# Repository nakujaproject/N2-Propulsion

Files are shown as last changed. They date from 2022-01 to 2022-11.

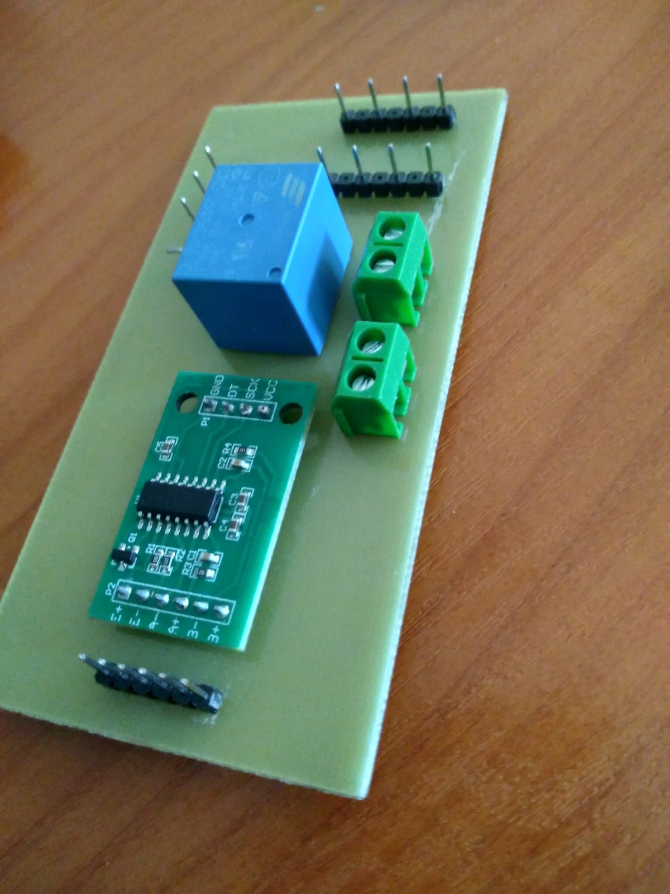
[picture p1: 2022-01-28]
Image gallery/Progress/soldered pcb.jpeg

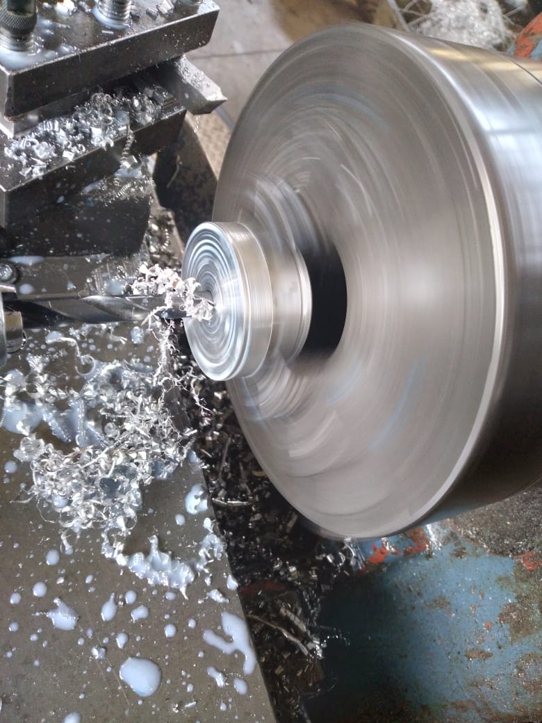
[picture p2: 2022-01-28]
Image gallery/Progress/bulkhead fab.jpeg

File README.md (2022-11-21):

# N2-Propulsion

This is project repo for the propulsion team containing all our design and simulations for the N-2 development

## General info

This project is where our design files for the nakuja N2 Propulsion are held. Different softwares are used for the purpose of development, such as;

* OpenMotor - Fuel Simulations
* Fusion 360 - CAD Designs & PCB Design
* Casing.xls - Excel spreadsheet for casing design parameters
* Ansys Fluent - Computational Fluid Dynamics

## Current directory structure

* **fuel** This contains all simulations for the N2 Fuel, the nozzle designs and casing designs.

* **Launch Pad** Contains all the designs of the lauch pad.

* **Test Stand** Contains the test stand designs, software and recorded data.

* **Important Software** Contains some of the important software used in design.

* **Resources** Contains the resources used in the development of the fuel.

## Pertinent information
* **Data Logging** The present calibration factor for the test stand is ___ .

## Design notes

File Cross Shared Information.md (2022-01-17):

# Cross Shared Information

* **Fuel Casing Outer Diameter**    -    54 mm
* **Fuel Length**                   -    *TBC*

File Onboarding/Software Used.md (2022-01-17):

# Used software

## Motor-Grain Performance simulation

Currently we are using [openMotor](https://github.com/reilleya/openMotor)

## Rocket flight performance

Currently we are using [Openrocket v15.03](https://github.com/openrocket/openrocket/releases/download/release-15.03/OpenRocket-15.03.jar)

## Computer Aided Design

Currently we are using [Inventor 2020](https://knowledge.autodesk.com/support/inventor/learn-explore/caas/CloudHelp/cloudhelp/2020/ENU/Inventor-WhatsNew/files/GUID-8126E8EE-422A-4DEF-9B14-513D87BD4122-htm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's,the%20release%20of%20Inventor%202020.&text=Inventor%202020%20delivers%3A,a%20modernized%20look%20and%20feel.)

## Analysis

For fluid analysis we are using [CFD 2019](https://knowledge.autodesk.com/support/cfd/troubleshooting/caas/downloads/content/autodesk-cfd-2019-download-and-install-help-documentation.html)

The Autodesk fusion version we are using is [Fusion 360](https://www.autodesk.com/products/fusion-360/free-trial)

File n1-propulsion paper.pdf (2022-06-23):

# Development of Solid Propellant Motor For Low Altitude Model Rockets

Abstract This paper describes the design, analysis, and testing of a solid propellant rocket motor designed to propel a model rocket to an apogee of 50 meters. The motor and the propulsion system had to be integrated into an airframe with a small payload thus had to provide enough thrust to reach the desired altitude yet remain compact and lightweight. All this had to be done with the constraint of only using locally sourced materials.
OpenMotor software was used in simulating the motor performance of the motor. ANSYS Fluent was used to analyze the flow within the motor chamber and nozzle. Data from static tests are presented in this paper for the different motor designs and fuels tested. Sugar was used as fuel in the rocket motor with variations being made on the sugar types: Sucrose and Dextrose. The oxidizer used was Potassium nitrate. The paper presents a comparison of the different fuels used as well as the methods used in the preparation.
The selected motor was able to produce an average thrust of 35 Newtons with a peak thrust of 48 Newtons, which was able to propel the rocket to an apogee of 34 meters.

Keywords Solid propellant, static fire test, thrust curve.

30 1. Introduction
Rocket launches are a common scenario in the present 32 day with giant companies like SpaceX and Blue Origin 33 competing to pioneer space exploration [1][2]. While 34 this technology is fascinating, it has been growing for 35 decades [3]. However, modern rocketry became more
pronounced in the 20th 36 | Century [4]. | Robert H. Goddard,
37 an American, conducted experiments with solid and 38 liquid rocket propellants. He managed to fly a liquid-39 propelled rocket to an altitude of 12.5 meters in 1926 40 [5]. Jack Parsons, an American aerospace engineer in 41 1942, invented modern solid rocket propellant rockets 42 [6]. He substituted double-base propellant with asphalt 43 and potassium perchlorate. Most recently, these 44 propellants have been used in orbital space flights and 45 as boosters on rockets.
46 Our rocket development team, the Nakuja project,seeks 47 to build a low altitude solid motor propellant rocket to 48 fly it to an altitude of 50 m. Because solid rocket motors 49 are safer to work with and can last longer without 50 degradation, they were the appropriate choice for this 51 research. In this study, we conduct simulations to find

52 out the appropriate mixtures and grain size to be cast in 53 the solid rocket motor.
54 Based on the parameters obtained from the simulation, 55 we design and cast the solid rocket motor. To enhance 56 the motor performance, we also fabricate the nozzle. 57 Finally, we test and analyze the propellant’s 58 performance.
59 2. | Simulation
60 | The simulation was conducted to visualize some
61 abstract concepts, generate design parameters, create 62 step-by-step progression for iterative design as well as 63 generate safety guidelines. Autodesk Inventor was used 64 to model casing design and material analysis [9]. This 65 was done by utilizing the finite element analysis feature of 66 Autodesk Inventor. There was a need to strike a balance 67 between weight and strength. The propellant performance 68 was simulated using OpenMotor with the parameters 69 shown in Table I. The set parameters resulted in a 70 nozzle cross section as shown in Fig. 1.
71
72 | Table I
73 | Simulation SETTINGS FOR Openmotor
Parameter | Value

Throat Diameter | 10 mm
Exit Diameter | 22 mm
Efficiency | 0.85
Divergence Half Angle | 15 degrees
Convergence Half Angle | 35 degrees
Throat Length | 5 mm
Slag Build-up coefficient | 0 (m•Pa)/s
Throat Erosion coefficient | 0 m/(Pa•s)
Expansion Ratio | 4.84
74

75

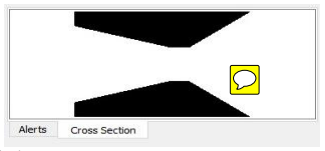
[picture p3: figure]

76 Fig 1. Nozzle cross-section designed by OpenMotor 77
78 The parameters of the propellant shown in Table I 79 include propellant grain length, grain diameter, and 80 combustion chamber diameter. A variation of these 81 parameters outlined the iterative construction and 82 testing path. The output of OpenMotor is a curve of the 83 instantaneous thrust against time as shown in Fig. 2. 84 This data coupled with the initial weight of the motor 85 and propellant are combined to form a .eng file. This 86 file can be used with OpenRocket to simulate rocket 87 flight.

88

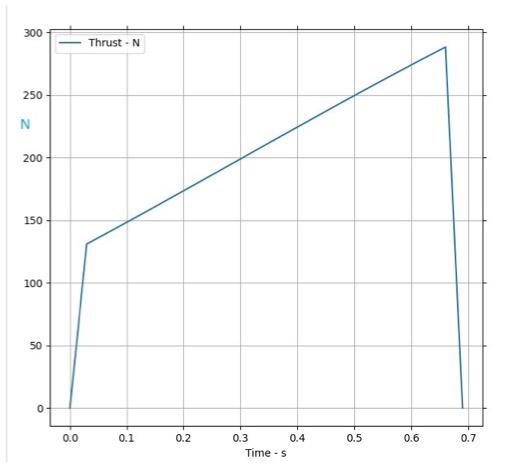
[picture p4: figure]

89 | Fig 2. Thrust curve generated by OpenMotor
90
91 The | various | motor | configurations | developed
92 throughout the iterative design process are illustrated in 93 Table II.
94
95 | | | Table II
96 | Imported .eng files from openRocket
Designatio | Total
n | Impulse (Ns)
Diamete | Lengt
r | h
(mm) | (mm)

F87
F46
F94
F65
F64
G47
G146
G108

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
G106 | 115 | 40 | 200
G152 | 119 | 40 | 200
G168 | 121 | 40 | 200
G117 | 131 | 40 | 200
G114 | 133 | 40 | 200
G186 | 140 | 40 | 200
97
98 Fig. 3 shows the simulated positioning of the motor 99 inside the rocket during simulation.
100

101

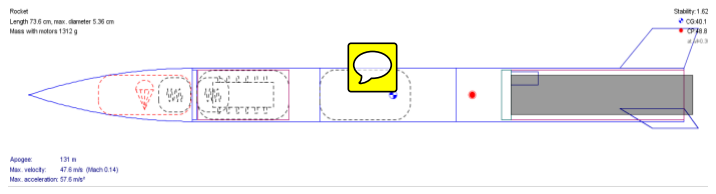
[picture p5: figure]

102 | Fig. 3. Image of rocket with the motor in place
103
104 The results from simulations conducted are highlighted 105 in Table III. The parameters that were critical to 106 development are the apogee and time of flight.
107
108 | Table III
109 | Simulation results from OpenRocket
Name | Apogee (m) | Time of flight (s)
V6- KNSU | 107 | 37.2
V6-KNSU-nozzled | 358 | 114
V7-KNSU | 134 | 45.4
V7-KNSU-nozzled | 450 | 142
V8-KNDX | 137 | 46.6
V8-KNDX-nozzled | 401 | 127
V9-KNDX | 134 | 45
110

111 3. Design
112 During iterative testing and development, the geometry 113 of the motor changed. The initial motor design was as 114 illustrated in Fig. 4.
115

116
117

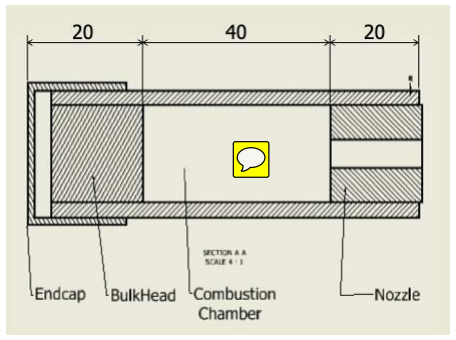
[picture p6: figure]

118 | Fig. 4. Initial motor design
119
120 | The final design of the motor was as illustrated in Fig.

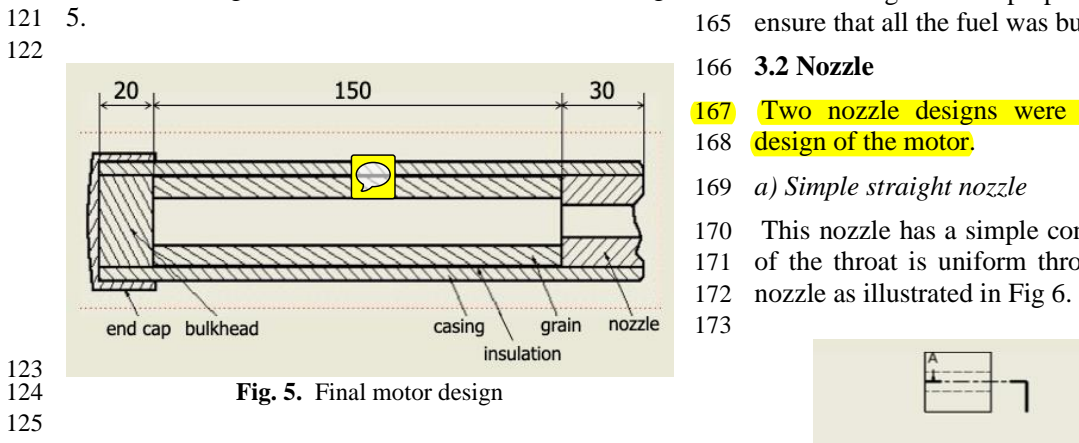
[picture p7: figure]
Fig. 5. Final motor design; 166 3.2 Nozzle; 168 design of the motor.; 169 a) Simple straight nozzle; 172 nozzle as illustrated in Fig 6. 173

126 | The different parts of the motor design can be broken
127 down as follows.

128 Casing

129 This part forms the body of the motor and is hollow to 130 accommodate the propellant grain and the nozzle. The 131 casing has some functional requirements, which 132 include; it should be able to withstand the high 133 temperatures and pressure of propellant combustion and
134 it | should | be | lightweight. | The | non-functional
135 requirements of the casing include that it should be 136 locally available and should be cheap to facilitate 137 iterative testing. The research was conducted on several 138 materials and two were shortlisted (i.e., Aluminum and 139 PVC). They both met the design requirements but PVC 140 was chosen, as it was cheaper, more readily available, 141 and easier to work with. The first iterations of the motor 142 used ¾-inch PVC pipe of various lengths. The length of 143 the final motor casing was chosen to be 200 mm. The 144 PVC pipe used was PN25 meaning it has a pressure 145 rating of 2.5 MPa. The pipe had an outer diameter of 40 146 mm and an inner diameter of 31 mm. The length of the 147 propellant grain heavily influenced this length. The 148 hollow tube would be capped by a PVC fitting called an

149 end cap and some hydraulic cement forming the 150 bulkhead. The other end of the hollow tube would house 151 the nozzle.

152 3.1 Propellant
153 The research was conducted and the team settled on 154 three possible propellants for development. All the 155 propellants had a simple combination of oxidizer, fuel, 156 and catalyst. For all the three propellants Potassium 157 Nitrate was chosen as the oxidizer and Iron III oxide 158 was chosen as the catalyst. Potassium Nitrate was 159 chosen because of its fair performance and availability. 160 The three propellants chosen were; 1. Potassium Nitrate 161 and Sucrose (KNSU) 2. Potassium Nitrate and Dextrose 162 (KNDX) 3. Potassium Nitrate and Sorbitol (KNSB). 163 The oxidizer to fuel ratio for all three fuels was 65 to 164 35. Meaning that the propellant was oxidizer rich to 165 ensure that all the fuel was burnt during combustion.
167 | Two nozzle designs were settled upon during the
170 | This nozzle has a simple construction as the diameter
171 of the throat is uniform throughout the length of the

174

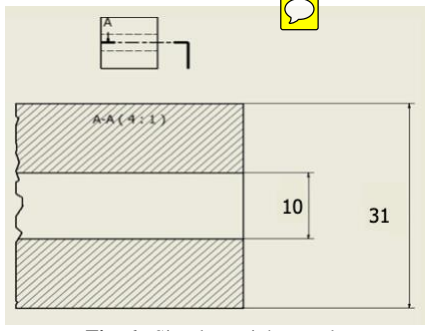
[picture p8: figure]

175 | Fig. 6. Simple straight nozzle
176 b) de Laval nozzle

177 This nozzle consists of a converging section, throat, 178 and diverging section as illustrated in Fig. 7 [10].
179

180

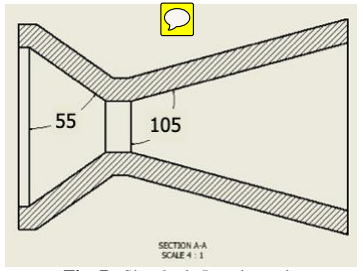
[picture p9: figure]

181 | Fig. 7. Simple de Laval nozzle
182
183 The converging section of the nozzle causes the gases 184 produced during combustion to accelerate linearly 185 towards the throat. At the throat, the gases achieve sonic 186 velocity and in the diverging section, the pressure of the 187 gases is reduced while conversely increasing the 188 velocity of the gases.

189 c) Nozzle CFD Analysis

190 A two-dimensional CFD analysis was carried out for 191 the nozzle design. From the resulting contours a
192 symmetry model was generated. Double precision was 193 used with 2 parallel processors selected. The solver 194 type was density-based and the flow was set to
195 axisymmetric. The energy equation was turned on and 196 the viscous model was set to k-epsilon (k-ϵ). To
197 simulate a turbulent flow k-ϵ (Realizable) viscous 198 model is used. The properties of the working fluid are 199 stated in Table IV.
200
201 | Table IV
202 | Properties of Air
Property | Air
Density | Ideal Gas
Specific Heat | 1006.43 (J/kg.K)
Thermal
conductivity

0.0242 (W/m.K)

Molecular Weight | 28.966 (kg/kmol)
Viscosity | Sutherland
203
204 The boundary conditions used are shown in Table V. 205
206 | Table V
207 | Boundary Conditions
Property | Value
Pressure inlet total gauge
pressure

2268000 (Pa)

Initial gauge pressure | 2267000 (Pa)
Inlet temperature | 1200 (K)
Pressure of operating
conditions

0 (Pa) (absolute)

Outlet pressure, Temperature 39365 (Pa), 243 (K) 208
209 A structured mesh was generated for the profile 210 resulting in 2587 nodes and 2410 elements. Face

211 meshing was applied on each of the five subsections 212 with adaptive sizing and a resolution of 7. The
213 resulting mesh is shown in Fig. 8.
214

215

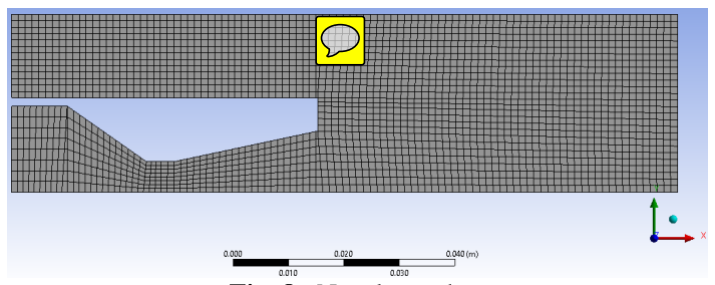
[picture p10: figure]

216 | Fig. 8. Nozzle mesh
217
218 The pressure contours generated are in Fig. 10. The 219 model used was k-ϵ. For gas, the pressure obtained for 220 the k-ϵ is 11.5% higher than the theoretical value [12]. 221

222

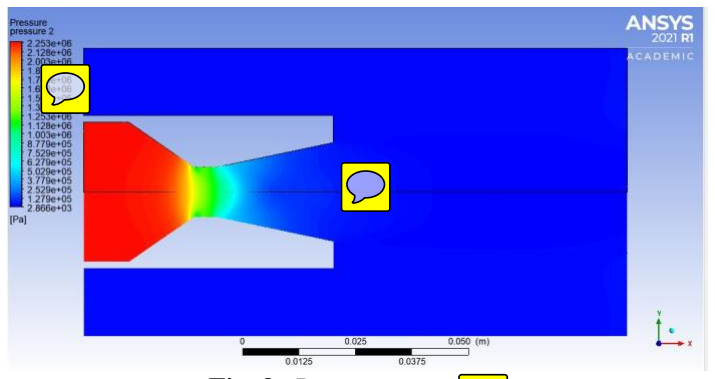
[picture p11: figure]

223 | Fig. 9. Pressure contour
224
225 From the results in Fig. 9, it was observed that the 226 pressure decreases from the convergent side of the 227 nozzle and no shocks are observed to form in the nozzle 228 which was ideal.
229 The contours generated for the velocity are shown in 230 Fig. 11. For Air velocity obtained in k-ϵ model, it is 231 2.5% lower than the theoretical value [12].
232

233

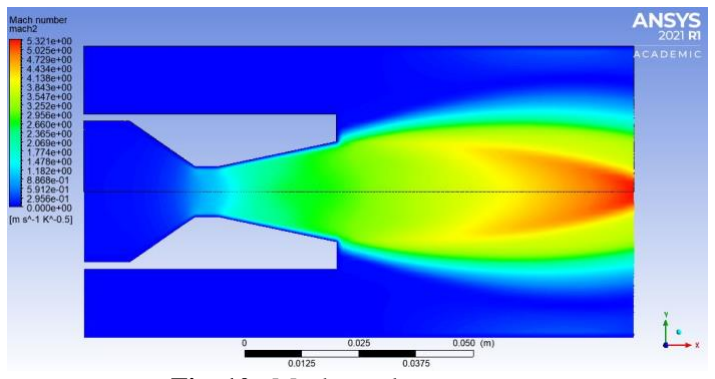
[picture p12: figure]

234 | Fig. 10. Mach number contour
235
236 The Mach number of the fluid as shown in Fig. 10 237 increases along the length of convergent-divergent 238 nozzles due to conservation of momentum in the fluid.

239 4. Fabrication

240 4.1 Casing

241 The casing was fabricated as follows: From V1 to V5 242 (earlier versions of the motor) the casing was made by 243 cutting to size a 3/4 inch PVC pipe. The length of the 244 pipe varied depending on the required geometry of the 245 specific motor. For later versions, the PVC pipe used 246 had an outer diameter of 40 mm with the length of each 247 being cut at 200 mm. The cut ends were smoothened 248 and squared using sanding paper.
249
250 4.2 Propellant
251 During the development, alterations were made to the 252 method of preparing the propellant. The process started 253 by obtaining the fuel and oxidizer. For sucrose we used 254 icing sugar as the particles are very small, for dextrose 255 we used glucose (dextrose monohydrate) and sorbitol 256 was obtained as sorbitol 70% solution. Potassium 257 Nitrate was obtained with a purity of 99% from local 258 chemical suppliers. Iron III oxide was obtained from a 259 chemical supplier at 99% purity. To obtain solid 260 sorbitol from the solution, the sorbitol solution was 261 heated in a pan using an electric heater for 15 minutes 262 at 150 degrees Celsius.
263 The weight of the required propellant was obtained 264 from OpenMotor. The solid components were first 265 blended using a blender and sieved to obtain the finest 266 particles. They were then weighed out using an 267 electronic scale and mixed in the ratio stated above 268 (65:35; O: F) the catalyst was added as 1 % of the 269 oxidizer and fuel mixture. The mixture was placed in a 270 plastic can and shaken vigorously. For sorbitol, the 271 solid obtained was in the form of a slurry and was used 272 as-is.
273 The first iterations of propellant development involved 274 dry packing this propellant mixture into the casing 275 using a mallet and a wooden rammer. The propellant 276 mixture was added in small amounts into the casing and 277 each time it was packed in using the rammer and the 278 mallet. When the desired height of the propellant was 279 achieved, a drill bit was used to create a combustion 280 chamber. The size of the combustion chamber 281 depended on the required grain geometry.
282 For further motors, the propellant grain was prepared 283 by casting. Casting involves heating the propellant 284 mixture until it melts and pouring it into a mold to 285 obtain the desired shape. The grain is left to solidify and 286 then removed from the casting apparatus. The casting 287 process was done using an electric heater, a pan, and 288 coring rods and tubes. A coring rod is a cylindrical piece 289 of metal with a chosen size all through. A coring tube is 290 made by cutting 150 mm of PVC pipe and then lining 291 the inside with cardboard paper. The paper serves as a

292 cover for the solid propellant as well as an insulator to 293 the casing during combustion.
294 The casting process began by preheating the pan and 295 then adding about half the propellant mixture to the pan. 296 Using a wooden spoon, the mixture was stirred until it 297 started to melt. More of the mixture was added at this 298 point. The propellant was heated to a casting 299 temperature of 145 °C for KNSU, 135 °C for KNSB and 300 KNDX. The propellant was then poured into the casting 301 tube and the coring tool was inserted to make a 302 combustion chamber. The coring tool was left in for a 303 sufficient time; 3 minutes for KNSU, 10 minutes for 304 KNDX, and 20 minutes for KNSB; until the propellant 305 began to solidify. At this point, the coring tool was 306 removed and the grain was left to cool in a desiccator. 307 The desiccator was constructed using a simple lunch 308 box in which a sufficient amount of Fused calcium 309 chloride was placed.
310 The grain was left to cool until it was fully solidified. 311 For KNSU it would take roughly 3 hours, for KNDX it 312 would take about 24 hours and for KNSB it would take 313 48 hours Once the grain had solidified it was ready for 314 firing. An image of the casting process is illustrated in 315 Fig 11.
316

317

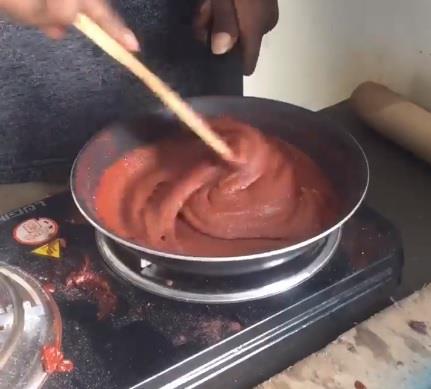
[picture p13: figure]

318 | Fig. 11. Casting process
319
320 The final grain obtained was red for all three propellant 321 types as a result of the Iron III oxide. Fig. 12 shows the 322 grain in the casting tube and casting case after removing 323 the coring rod.
324

325

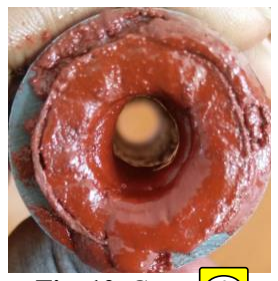
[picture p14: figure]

326 | Fig. 12. Cast grain
327 4.3 Nozzle
328 Both the straight and de Laval nozzles were made using

329 hydraulic cement. The cement is fast setting and only 330 requires to be mixed with water.

331 a) Straight nozzle

332 The straight nozzle was constructed by placing a finite 333 amount of cement into an open end of the cut PVC pipe 334 and letting it solidify. A drill bit was then used to make 335 a hole of the required diameter in the cement.

336 b) de Laval nozzle

337 This nozzle was first made by painting the inside of the 338 casing with acrylic paint. This was done to enhance the 339 cohesion of the hydraulic cement and the walls of the 340 PVC pipe. The paint was allowed to dry overnight. The 341 converging side was made using a 3D printed part 342 displayed in Fig. 13.
343

344

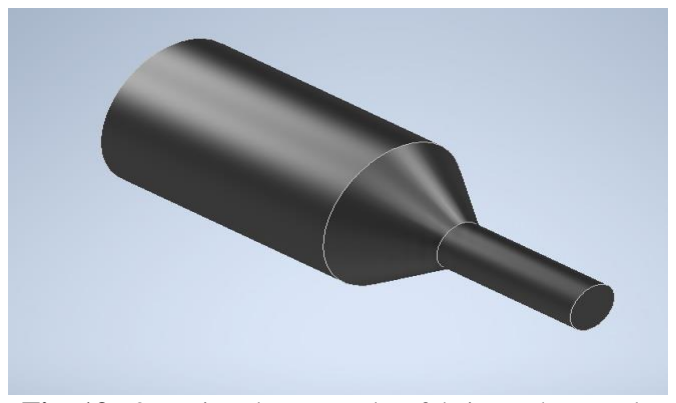
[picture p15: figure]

345 Fig. 13. 3D printed part used to fabricate the nozzle 346
347 The cement was first mixed with water. The part was 348 pushed in through the unpainted side until the tip of the 349 part was flush with the painted end of the pipe. The 350 cement was then poured onto the cavity formed and 351 then allowed about 3 minutes to solidify. The piece was 352 then forced out using a screwdriver and a hammer. The 353 diverging side was made by using a scraper to remove 354 the cement until the required angle of 15 degrees was 355 obtained. The completed nozzle was as shown in Fig. 356 14.
357

358

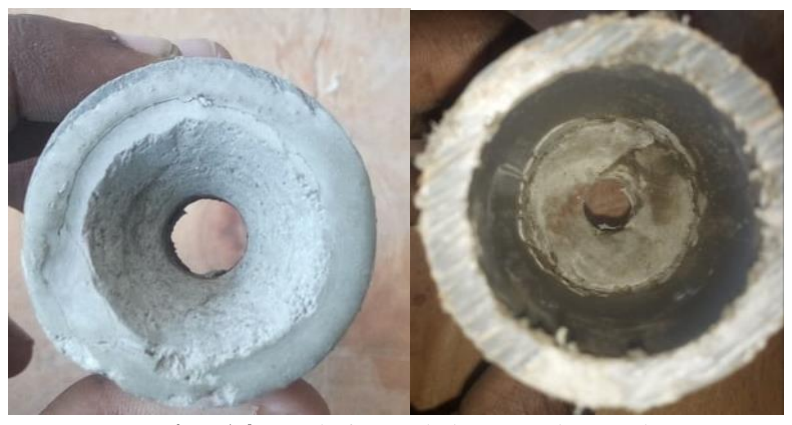
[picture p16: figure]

359 | Fig. 14. Fabricated de Laval nozzle
360 | (left: diverging side, right: converging side)
361
362 4.4 Assembly
363 The assembly of the motor was done by first 364 constructing the nozzle as described above. The grain

365 obtained after casting was placed in the casing with the 366 constructed nozzle. The open end of the casing was then 367 sealed with hydraulic cement. To reinforce this a PVC 368 end was added. The PVC end cap is a PVC fitting of an 369 internal diameter of 40 mm and an external diameter of 370 50 mm. The end cap was attached using PVC tangit 371 glue. The external surface of the casing was buffed 372 using sandpaper and the ends were made square. Tangit 373 glue was applied to the casing and the internal side of 374 the end cap. The two were then assembled and held in 375 position tightly for about one minute. The assembly was 376 left to cure for about two hours before any firing could 377 take place. The assembly was as illustrated in Fig. 15. 378

379

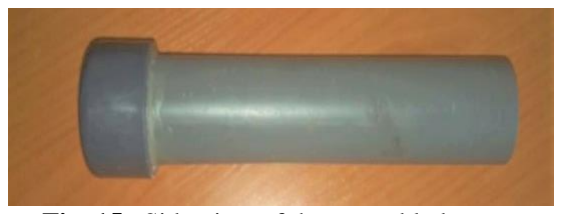
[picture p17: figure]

380 | Fig. 15. Side view of the assembled motor

381 5. Testing
382 Testing was conducted to generate the motor thrust 383 curves. Testing was conducted in the form of static 384 firing tests. The tests were conducted using a vertical 385 static fire test stand fabricated from mild steel due to its 386 high dynamic yield strength under high-velocity impact 387 [8]. The thrust measurement apparatus consisted of four 388 pin-load cells in a Wheatstone Bridge circuit with a 389 maximum load capacity of 200 kilograms, an HX711 390 load cell amplifier with a sampling frequency of 80 Hz, 391 and a 10-bit A/D converter of Arduino. The unit used a 392 bench vice to hold the motor in place with the load cells 393 mounted on mild steel bars below the bench vice. The 394 system was calibrated using a reference weight. The test 395 stand assembly is shown in Fig. 16, the data collection 396 pipeline in Fig. 17, and the remote ignition system in 397 Fig. 18.
398

399

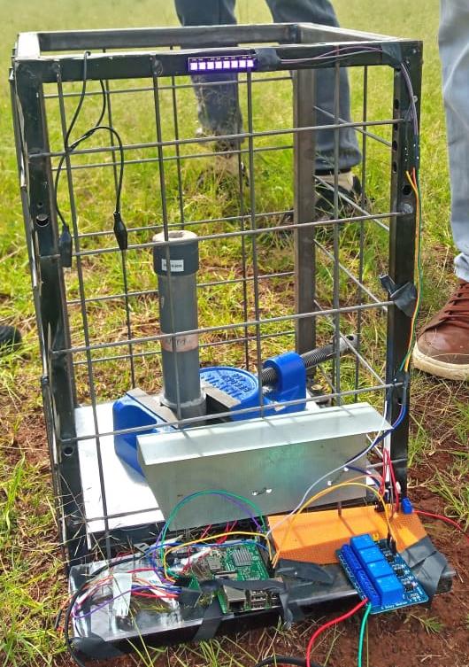
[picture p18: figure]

400 | Fig. 16. Static fire test stand assembly with solid rocket
401 | motor
402

403

404 | Fig. 17. Diagram of data collection

405

406 | Fig. 18. Test stand remote ignition sequence
407
408
409 The remote ignition system consisted of an igniter 410 placed through the nozzle of the motor reaching the 411 combustion chamber. The purpose of the igniter was to 412 convert an electrical signal from the 9V battery to heat 413 which would ignite the propellant in the motor. The 414 igniter we used for testing consisted of nichrome wire, 415 10 mm diameter straws, and black powder shown in 416 Fig. 19. One end of the straws was sealed using hot glue. 417 The straw was then filled with black powder. Nichrome 418 wire with leads attached to it was then placed in contact 419 with the black powder. This was done carefully so that 420 the nichrome was in contact with the black powder but 421 did not short itself or the lead wires.
422

423

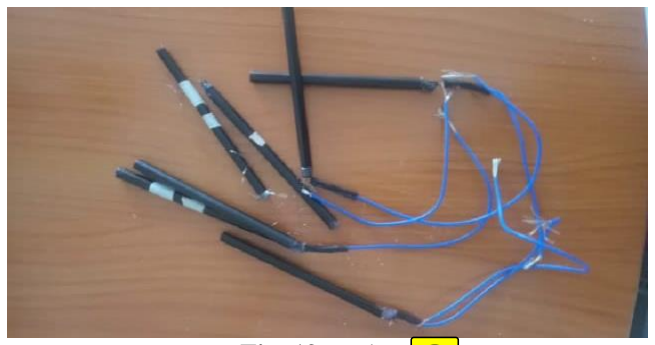
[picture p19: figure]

424 | Fig. 19. Igniters

425 6. Results

426 Prototype motors

427 The first set of motors were 4 variations of the same 428 grain diameter and grain length with variations in the 429 core diameter.
430 The 4 motor variants had 2 propellant compositions: 431 KNDX and KNSU. The variation between them was 432 different core diameters to explore the effect of
433 chamber pressure on motor performance. The KNSU 434 motors were designated V7 and V8 while the KNDX 435 motors were designated V9 and V10. The thrust curves 436 of V6 and V7 are as shown in Fig. 20. The V9 and 437 V10 variants of the propellant failed to ignite during 438 the static firing test and thus could not be evaluated.

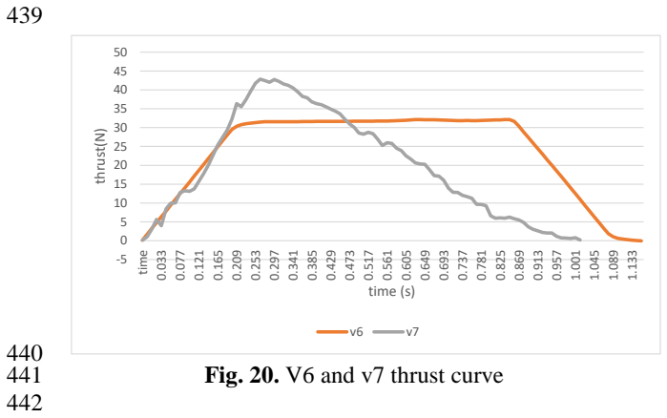
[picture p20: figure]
time; thrust(N); time (s)

441 | Fig. 20. V6 and v7 thrust curve

443 Final Motor

444 Improvements were made to the V7 prototype motor 445 to include a nozzle to optimize motor performance as 446 shown in Fig. 21.

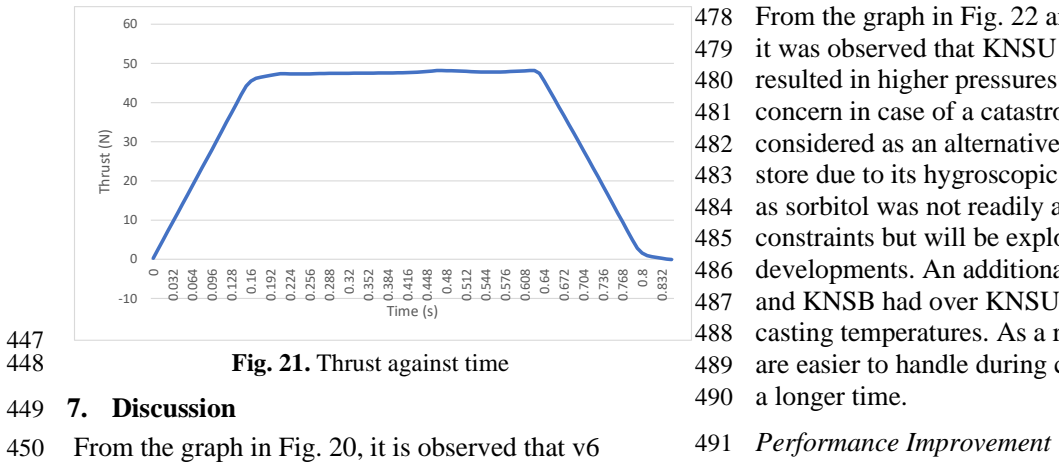
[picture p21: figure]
Fig. 21. Thrust against time; 449 7. Discussion; 490 a longer time.; 491 Performance Improvement; Thrust (N); Time (s)

450 From the graph in Fig. 20, it is observed that v6
451 maintains a neutral ideal curve while V7 has a high 452 peak followed by a rapid drop in thrust. This occurred 453 in V7 as during the static firing test a failure occurred 454 in the bulkhead leading to a drop in chamber pressure 455 thus the observed drop in performance. It was however

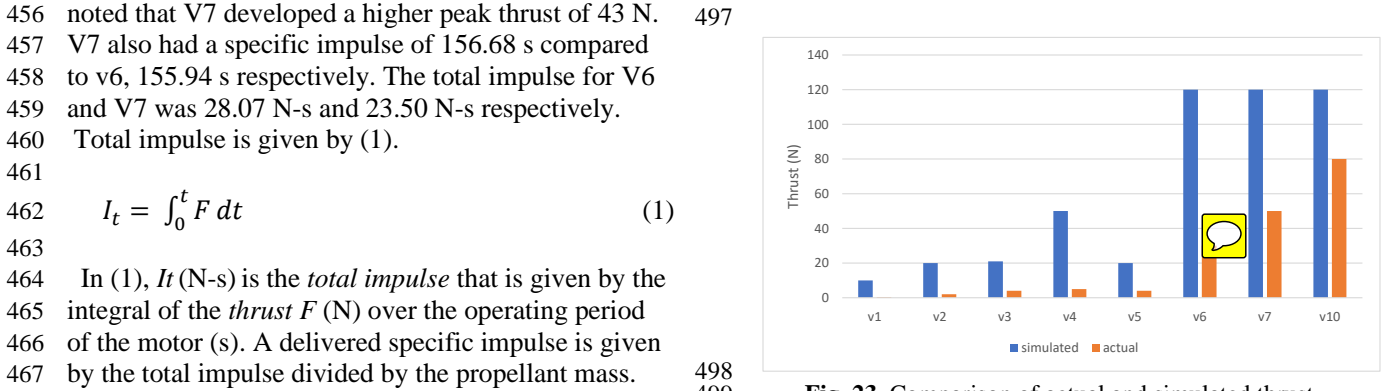
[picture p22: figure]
Thrust (N); simulated; actual

456 noted that V7 developed a higher peak thrust of 43 N. 457 V7 also had a specific impulse of 156.68 s compared 458 to v6, 155.94 s respectively. The total impulse for V6 459 and V7 was 28.07 N-s and 23.50 N-s respectively. 460 Total impulse is given by (1).
461
| It = ∫ F t
| 0
464 | In (1), It (N-s) is the total impulse that is given by the
465 integral of the thrust F (N) over the operating period 466 of the motor (s). A delivered specific impulse is given 467 by the total impulse divided by the propellant mass.

468 Final Motor

469 The peak thrust generated was 48 Newtons, with a 470 total impulse of 31.32 N-s and a specific impulse of 471 164.82 s, and an average thrust of 35.09 N.

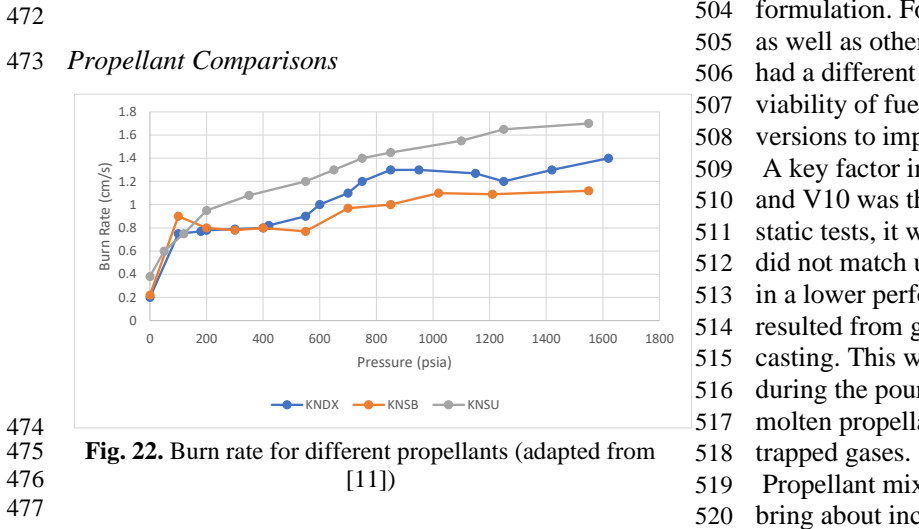
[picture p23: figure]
473 Propellant Comparisons; 518 trapped gases.; Burn Rate (cm/s); Pressure (psia); KNDX; KNSB; KNSU

475 Fig. 22. Burn rate for different propellants (adapted from

478 From the graph in Fig. 22 and experiments carried out 479 it was observed that KNSU had a higher burn rate but 480 resulted in higher pressures which were a safety
481 concern in case of a catastrophic failure. KNDX was 482 considered as an alternative but it proved difficult to 483 store due to its hygroscopic nature. KNSB was left out 484 as sorbitol was not readily available in the given time 485 constraints but will be explored in future
486 developments. An additional advantage that KNDX 487 and KNSB had over KNSU was that they had lower 488 casting temperatures. As a result, KNDX and KNSB 489 are easier to handle during casting and remain fluid for

492 An important takeaway was the overall incremental 493 performance of the rocket motor for the static tests 494 carried out. This is best characterized by the
495 comparison between the actual and simulated peak 496 thrust as shown in Fig. 23.
499 | Fig. 23. Comparison of actual and simulated thrust
500
501 The versions V1-V5 differ in size to the V6-V10 502 hence the difference. The propellants in V1-V5 also 503 don’t include a catalyst (Iron oxide) in their
504 formulation. For V6-V10, the grain length is the same 505 as well as other factors only differing in V10 which 506 had a different nozzle. V1-V5 were used to test the 507 viability of fuel used and were set aside for latter
508 versions to improve on performance.
509 A key factor in improving performance between V6 510 and V10 was the improvement in grain density. During 511 static tests, it was noted that the simulated grain mass 512 did not match up to the actual value. This would result 513 in a lower performance than expected. This might have 514 resulted from gas porosity during the pouring stage of 515 casting. This was solved by improving compacting 516 during the pouring stage of casting by ramming the 517 molten propellant to fill up available space and expel

519 Propellant mixing processes were also enhanced to 520 bring about increased performance. The propellants 521 were sifted to remove large particles after being

522 ground using a blender. Dry mixing was also enhanced 523 with shaking in a container for extended periods.
524 Smaller particles and close mixing meant that the
525 oxidizer and fuel had closer contact resulting in a more 526 effective reaction.
527 The V10 and V7 differ in the nozzle utilized. The 528 convergent-divergent nozzle developed brought about 529 increased performance due to the increased velocity of 530 exhaust gases due to pressure reduction from the
531 converging side of the nozzle to the diverging as a 532 result of energy conservation. This resulted in
533 improved performance compared to the straight nozzle 534 initially used.

535 8. Conclusions
536 By analyzing the thrust curves obtained from the static 537 fire tests of KNSU and KNDX, this study established 538 that for a given mass of solid rocket motor propellant, 539 KNSU generated more thrust and demonstrated a 540 higher burning rate compared to KNDX. However, 541 KNDX has a bigger safety margin compared to KNSU 542 because of its lower chamber pressure. Additionally, 543 analysis results showed that grain inclusions, in
544 particular, air bubbles, negatively influence the thrust 545 performance of both KNSU and KNDX. Concerning 546 the propellant development method, tests on the
547 propellants considered in this study showed that dry 548 heating produces a homogenous grain structure. The 549 post-burning analysis showed better combustion 550 efficiency of KNSU compared with KNDX. The 551 important role of catalysts has been shown. In
552 particular, the addition of Iron (III) oxide during the 553 casting process resulted in a significant increase in the 554 burn rate and the amount of burned propellant for both 555 sucrose and dextrose-based propellants.
556 Future research into solid rocket motor propellants for 557 model rockets should focus on determining ways of 558 optimizing the performance of sugar-based rocket 559 propellants such as KNSU and KNDX by for example 560 using additives. There is also a need to replace KNO3 561 with high-performance biodegradable oxidizers and 562 minimize plastic deformation of the PVC casing
563 during combustion. Additionally, while this paper 564 examines the performance of KNSU and KNDX 565 rocket propellants, further experimental and
566 observational studies are required to gain more insight

567 into the factors affecting the performance of KNDX 568 and KNSU propellants.

569 Acknowledgement
570 The authors thank Jomo Kenyatta University of 571 Agriculture and Technology for the use of the 572 Integrated Prototyping and Innovation Center. The 573 authors also acknowledge the financial support of the 574 AFRICA-ai-JAPAN Project (JICA) and the technical 575 support of Mr. Ben Maniafu.

576 References

577 | [1] M. Vozoff and J. Couluris, “SpaceX products-advancing
578 | the use of space,” in AIAA SPACE 2008 conference &
579 | exposition, 2008, p. 7836.
580 | [2] J. T. Smith, “The Future of Space Exploration: SpaceX’s
581 | Petitions for Inter Partes Review against Blue Origin’s
582 | Rocket-Landing Technology,” SMU Sci. & Tech. L. Rev.,
583 | vol. 19, p. 65, 2016.
584 | [3] L. T. DeLuca, “Highlights of solid rocket propulsion
585 | history,” in Chemical Rocket Propulsion, Springer, 2017,
586 | pp. 1015–1032.
587 | [4] D. A. Singh, “Sugar Based Rocket Propulsion System-
588 | Making, Analysis & Limitations,” vol. 2, no. 5, p. 8,
589 | 2015.
590 | [5] S. Helmy and A. Helmy, “The Origins and Growth of
591 | Short Range Liquid Propellant Ballistic Rockets,” in
592 | AIAA Propulsion and Energy 2020 Forum, 2020, p.
593 | 3792.
594 | [6] P. Umholtz, “The history of solid rocket propulsion and
595 | Aerojet,” 35th Joint Propulsion Conference and Exhibit,
596 | 1999.
597 | [7] W. R. Dornberger, “The German V-2,” Technology and
598 | Culture, vol. 4, no. 4, pp. 393–409, 1963.
599 | [8] M. Singh et al., “Dynamic yield strength of mild steel
600 | under impact loading,” Defence Science Journal, vol. 58,
601 | no. 2, p. 275, 2008.
602 | [9] L. A. N. Wibawa, K. Diharjo, W. W. Raharjo, and B. H.
603 | Jihad, “Stress Analysis of Thick-Walled Cylinder for
604 | Rocket Motor Case under Internal Pressure,” Journal of
605 | Advanced Research in Fluid Mechanics and Thermal
606 | Sciences, vol. 70, no. 2, Art. no. 2, 2020.
607 | [10] N. K. Mishra and D. S. S. Prasad, “MODELING &
608 | SIMULATION OF ROCKET NOZZLE,” vol. 2, no.
609 | 2309, p. 8, 2014.
610 | [11] ‘Richard Nakka’s Experimental Rocketry Web Site’. (https://www.nakka-rocketry.net/sorb.html)
611 | https://www.nakka-rocketry.net/sorb.html (accessed Jul.
612 | 12, 2021).
613 | [12] V. A. Hemanth and U. S. Jyothi, ‘CFD Analysis of a Solid
614 | Propellant Retro Rocket Motor using Ansys Fluent’, in
615 | E3S Web of Conferences, 2020, vol. 184, p. 01054.187(2),
616 | pp. 507-516, 2001.
617

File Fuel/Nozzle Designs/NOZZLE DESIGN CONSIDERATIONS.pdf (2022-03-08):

NOZZLE DESIGN CONSIDERATIONS In the design of the Solid Rocket Motor, the design of the nozzle is of critical importance. This document highlights the procedures taken in the design of the nozzle for the N-2 rocket motor.
The specifications for the N-2 rocket motor were as follows;
1. Fuel casing outer diameter → 56 mm
2. Fuel to be used → KNSB (Potassium Nitrate + Sorbitol) Tools Used
1. OpenMotor
2. Casing.xls
3. SRM.xls

Procedure
1. Using the excel sheet casing.xls, we get the Design pressure for the rocket motor casing as well as the burst pressure.

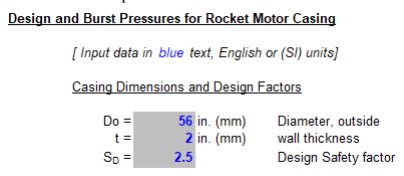
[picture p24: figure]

The values for the outer diameter and thickness of the proposed casing are input, in mm. The safety factor being 2.5

The material properties are also input in the following sections. N-2 utilizes 7075 aluminum alloy for the fabrication of the casing, the values are input in the sections below.

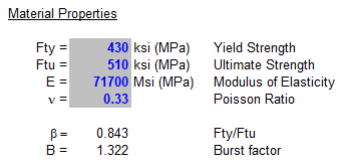
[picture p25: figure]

The tool computes the design and burst pressures that can be handled by the casing with the given dimensions. The results are presented below;

The design pressure is 12 MPa.
However, the initial design was done using 6063 aluminum which was not locally available. Using 6063 aluminum yielded a Design pressure of 2 MPa.
This value of pressure was used since it still lies way below the design pressure of 7075 aluminum, i.e., 12 MPa.
The value of interest is the design pressure → 2MPa. (Remember to use the design pressure obtained from the tool casing.xls)
2. Using the excel workbook SRM.xls, we get the design of the nozzle as follows.
In the first sheet within the workbook, Data and Kn, the values for Outer grain diameter, core diameter, number of grain segments, segment lengths, type of fuel, inhibited surfaces are input according to the design parameters.
The target maximum pressure is also input in psi.
The values were input as shown below;

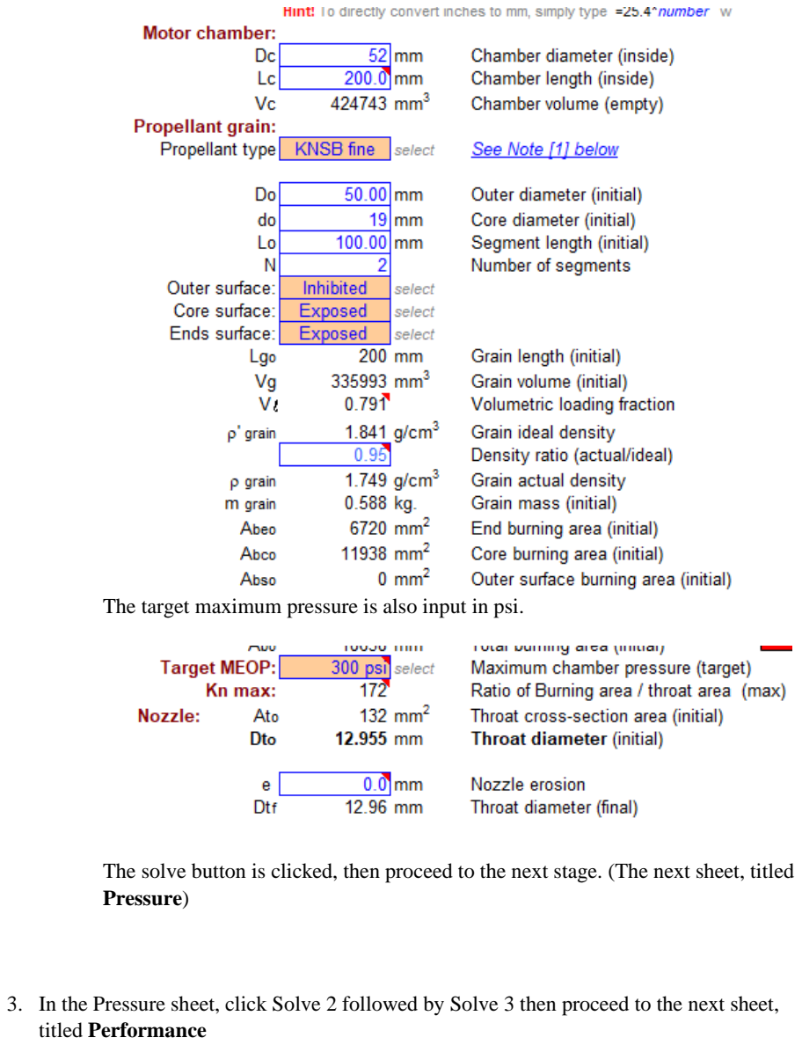
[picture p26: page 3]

The target maximum pressure is also input in psi.

The solve button is clicked, then proceed to the next stage. (The next sheet, titled Pressure)

3. In the Pressure sheet, click Solve 2 followed by Solve 3 then proceed to the next sheet, titled Performance

4. In the Performance sheet, the nozzle efficiency and the nozzle expansion ratio are set. Optimum values for the Nozzle expansion ratio are given and a suitable value for the nozzle expansion ratio can be selected bearing this in mind.


Values for the optimum nozzle expansion ratio at Po max and the average optimum nozzle expansion ratio. These values are computed for the specific fuel we have been designing. In this case, the value 6.25 is selected. 6.25 is arbitrarily selected since it lies close to the optimum values provided. Any value around the given optimum values can be used.

5. Once this is done, click the Solve (4) button and proceed to the next excel sheet, titled Nozzle Design.
Here, the convergence and divergence half angles are selected within some allowable limits. In our case, the following angles were selected.


6. The final output of the rocket motor is then displayed in the next sheet, titled Output This is shown below;


From Section (5) above, the nozzle parameters can be obtained.
The section included the parameters to be used for the nozzle fabrication. These parameters are listed below.

These values are used to design the nozzle.

The Nozzle Engineering drawing is attached below

OpenMotor is used to verify all these values and further optimize the nozzle if need be.

Dept.; Technical reference; Created by; Approved by; Document type; Document status; Title; DWG No.; Rev.; Date of issue; Sheet; Optimum Nozzle v3; Washington Kamadi; A-A (2:1) Ø⁵⁰; Ø³⁰

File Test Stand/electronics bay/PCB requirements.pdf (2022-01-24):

# NAKUJA PROJECT PROPULSION TEST STAND PCBS

### IGNITION PCB

Purposes
1. Ignition of the fuel
2. Provide redundancy to ensure several options for ignition.
3. Provide power for the raspberry pi
Requirements
1. Use a signal from the raspberry pi to turn on and off a relay module.
2. Provide power for the raspberry pi from the available 12 V
3. Provide power for the Arduino

### DATA LOGGING PCB

Purposes
1. Ensure data flow from the load cells to the load cell amplifier
2. Ensure data flow from the load cell amplifier to the Arduino board
Requirements
1. Have a compact connection between the wires from the load cells to the amplifier.
2. Have connection between the amplifier and the Arduino via header pins.

Useful info
1. Load cell amplifier is known as hx711. (https://www.pixelelectric.com/sensors/load-pressure-flow-vibration/load-pressure-force-flex-sensor/hx711-load-cell-amplifier/) Found on the link shown.
2. The PCBs should not exceed 50 mm by 50 mm
3. Both PCBs will be embedded on one PCB to make them compact.

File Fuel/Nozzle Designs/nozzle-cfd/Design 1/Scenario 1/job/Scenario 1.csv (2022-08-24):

CPU time | 1.794
memory | 58527744
fluid nodes | 4721
solid nodes | 105
fluid elements | 12211
solid elements | 2503

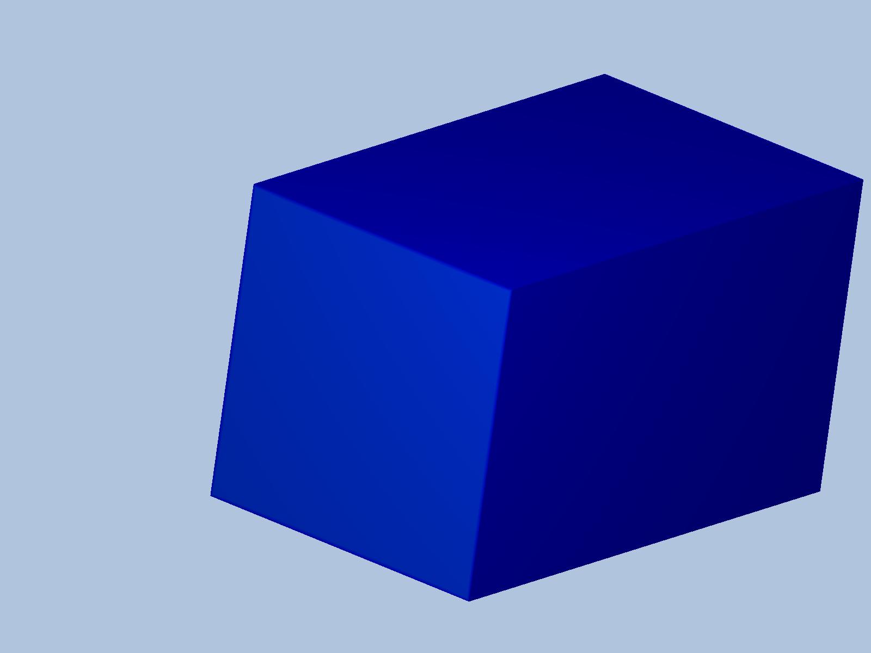
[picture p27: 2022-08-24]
Fuel/Nozzle Designs/nozzle-cfd/preview.jpg

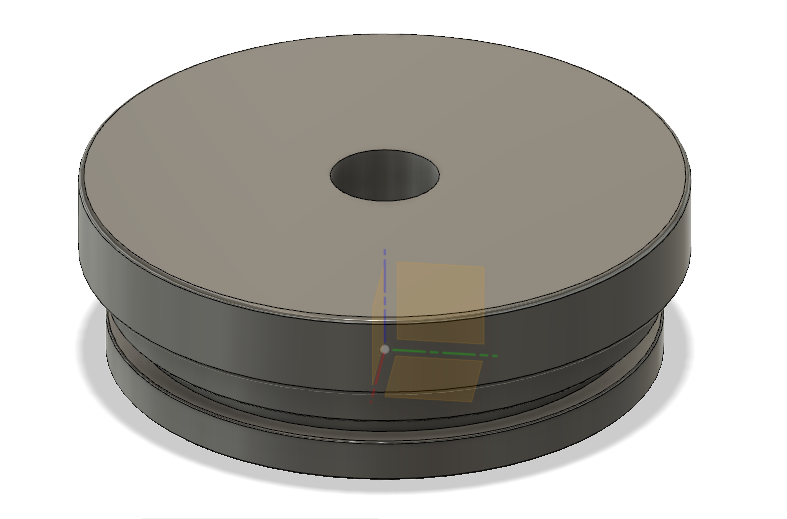
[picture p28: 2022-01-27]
Image gallery/Simulation data/Bulkhead/Bulkhead Design.png

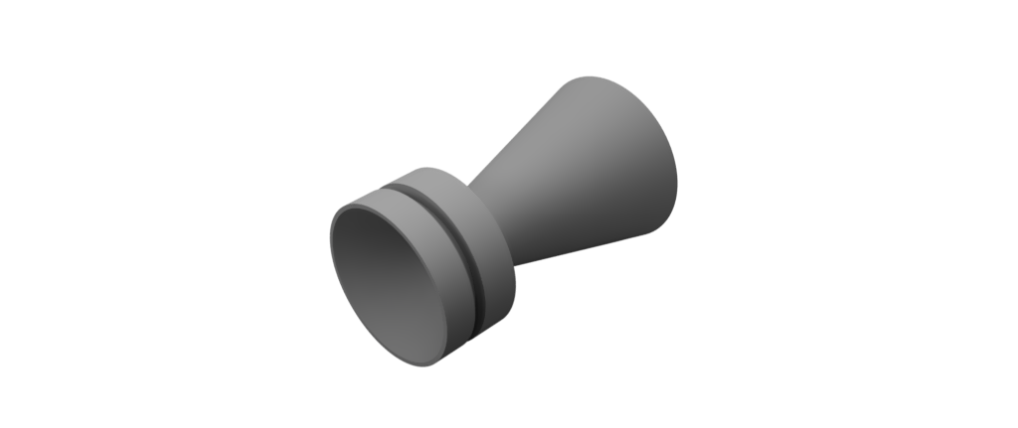
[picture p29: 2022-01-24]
Fuel/Nozzle Designs/NOZZLE.png

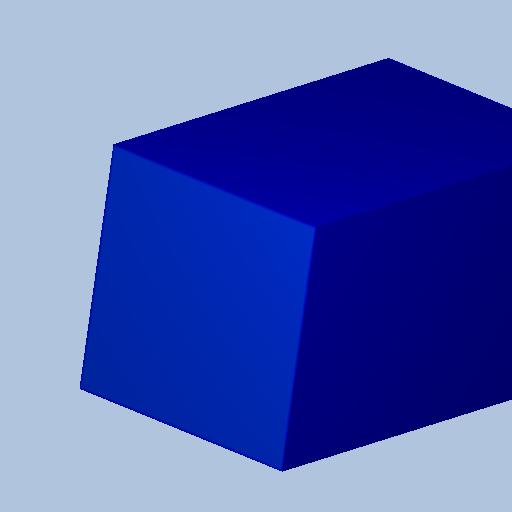
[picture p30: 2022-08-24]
Fuel/Nozzle Designs/nozzle-cfd/Design 1/Scenario 1/thumbnail.jpg

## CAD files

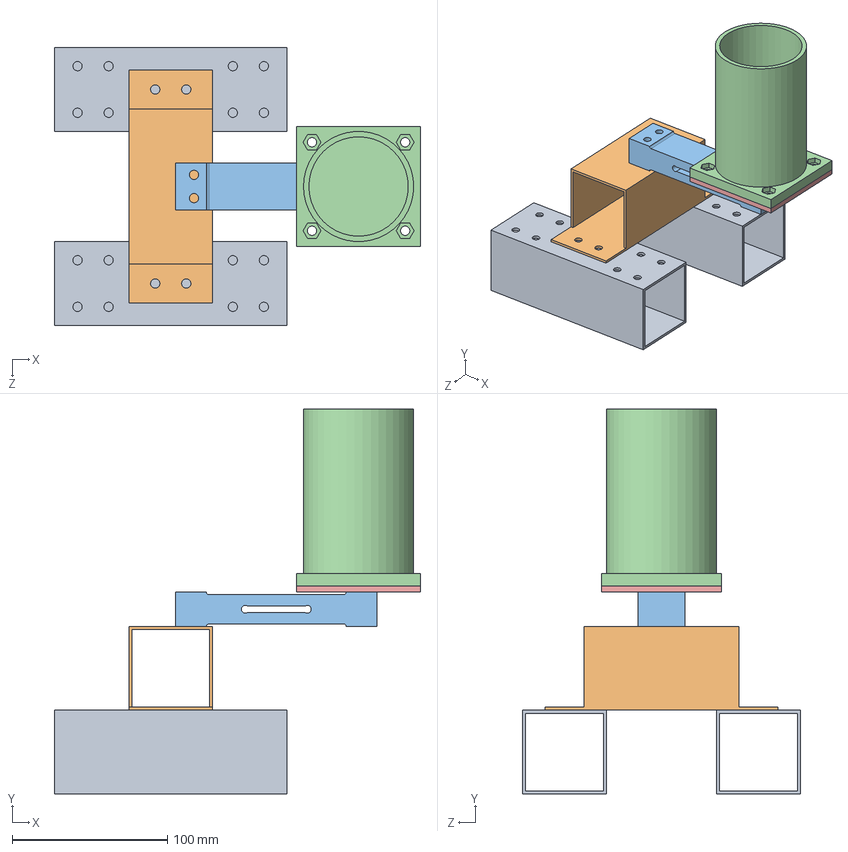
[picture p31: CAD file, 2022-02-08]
Test Stand/CAD design/test stand v2.SLDASM
236.0 x 248.0 x 179.0 mm
SHS Aluminum x 2
Cut SHS
load cell
thrust plate v2
thrust base

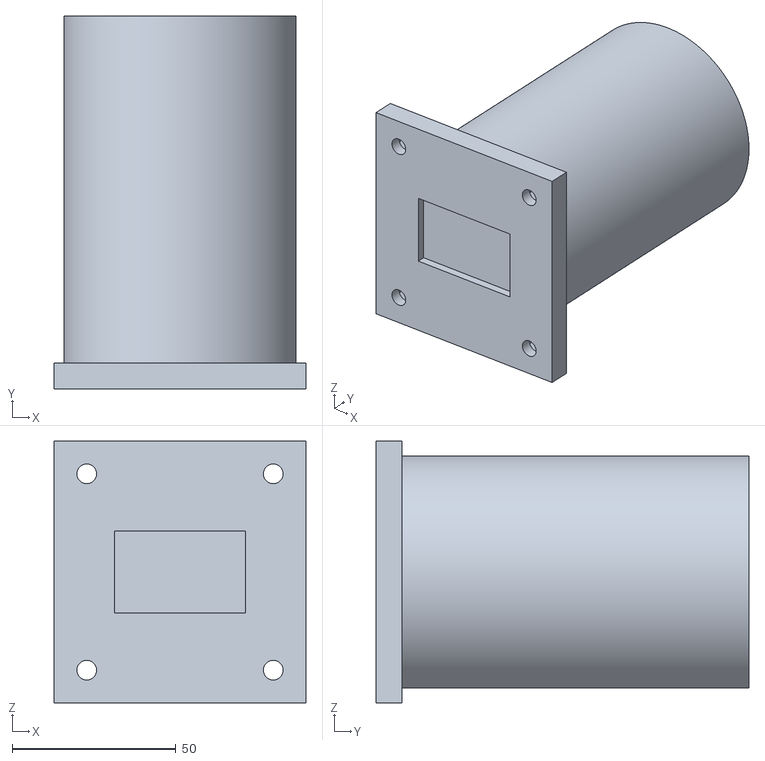
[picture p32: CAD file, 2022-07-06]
Test Stand/CAD design/thrust plate v3.STL
77.0 x 114.0 x 80.0

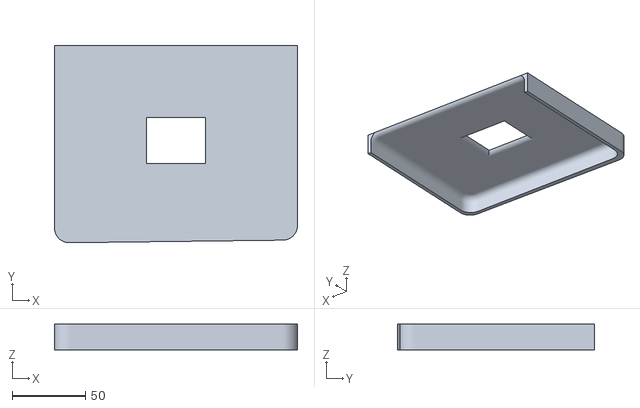
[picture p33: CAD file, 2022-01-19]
Test Stand/electronics bay/Cover v3.stl
166.0 x 134.9 x 17.5

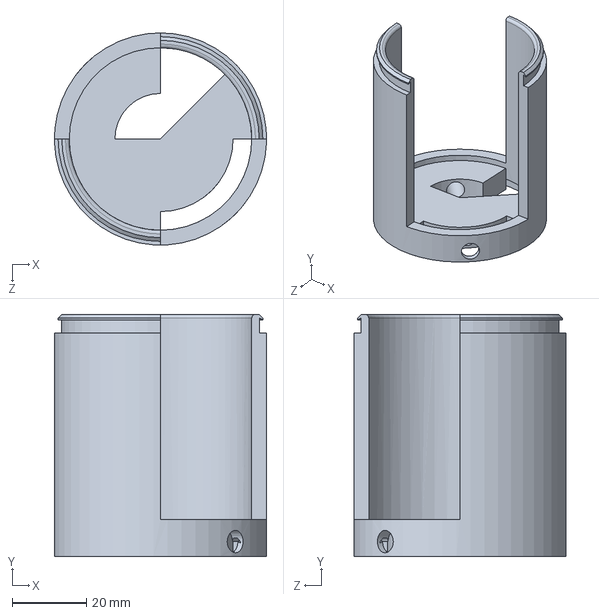
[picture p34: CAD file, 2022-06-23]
Test-Launch/Rocket Skeleton.SLDPRT
57.0 x 65.0 x 57.0 mm

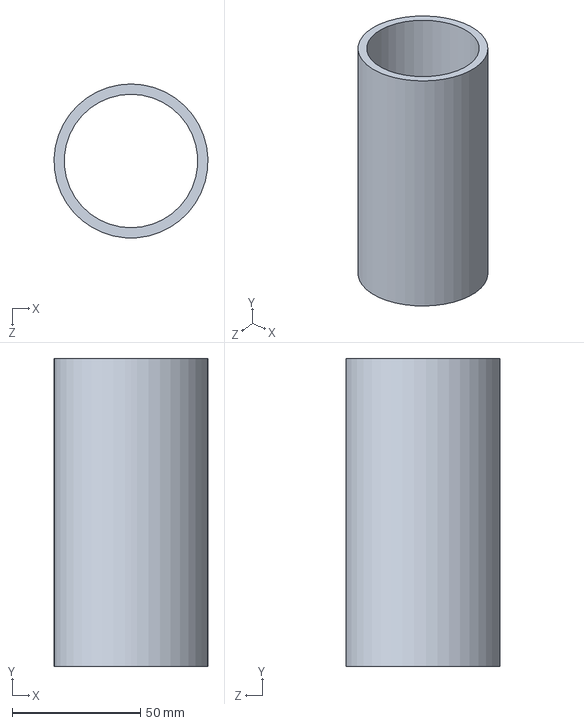
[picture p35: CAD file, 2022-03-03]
Fuel/Casting/Casting tools/casting cylinder.SLDPRT
60.0 x 120.0 x 60.0 mm

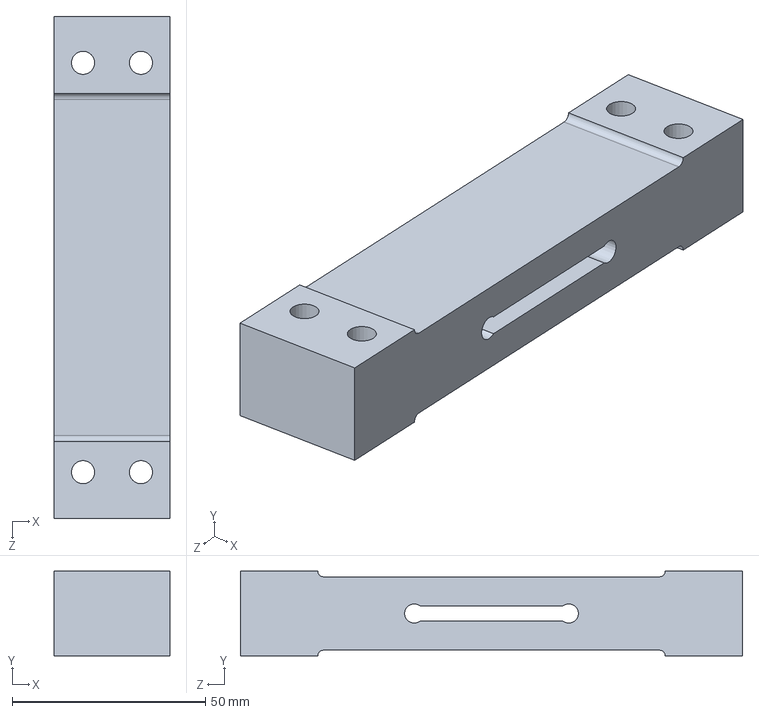
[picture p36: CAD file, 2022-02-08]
Test Stand/CAD design/load cell.SLDPRT
30.0 x 22.0 x 130.0 mm

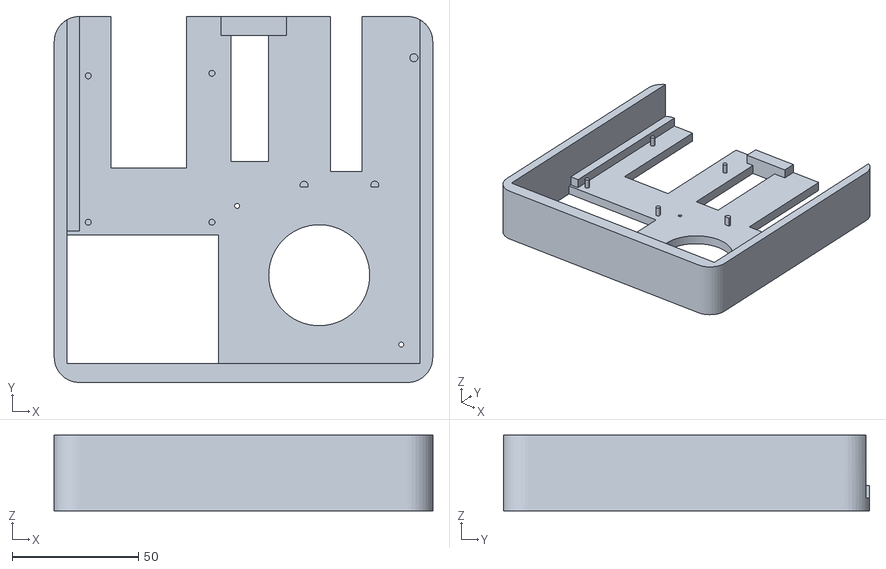
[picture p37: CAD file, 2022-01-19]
Test Stand/electronics bay/Electronics bay v16.stl
150.0 x 145.0 x 30.0

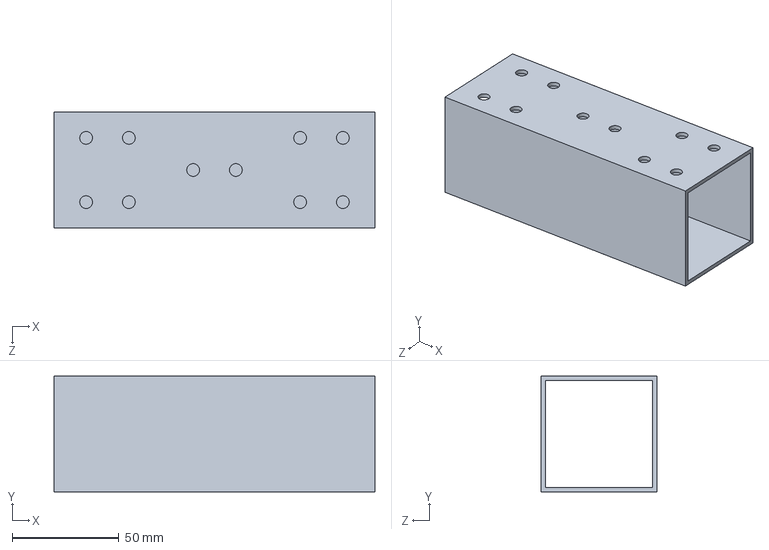
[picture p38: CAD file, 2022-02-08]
Test Stand/CAD design/SHS Aluminum.SLDPRT
150.0 x 54.0 x 54.0 mm

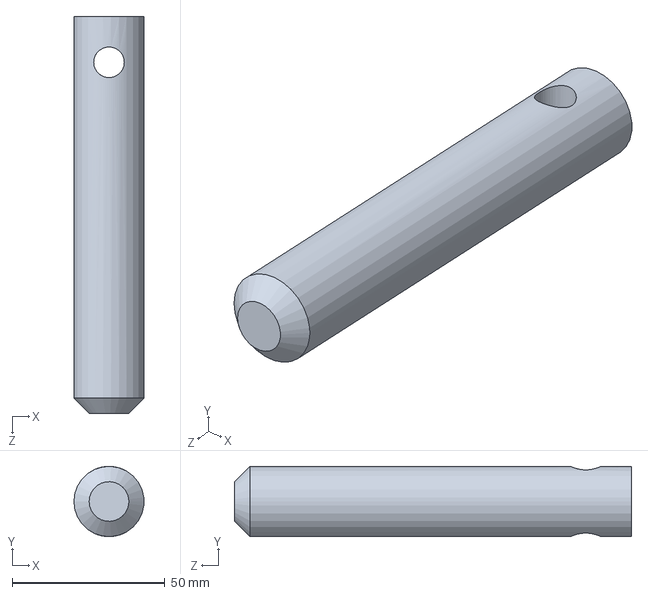
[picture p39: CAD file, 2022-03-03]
Fuel/Casting/Casting tools/Coring rod.SLDPRT
23.0 x 23.0 x 130.0 mm

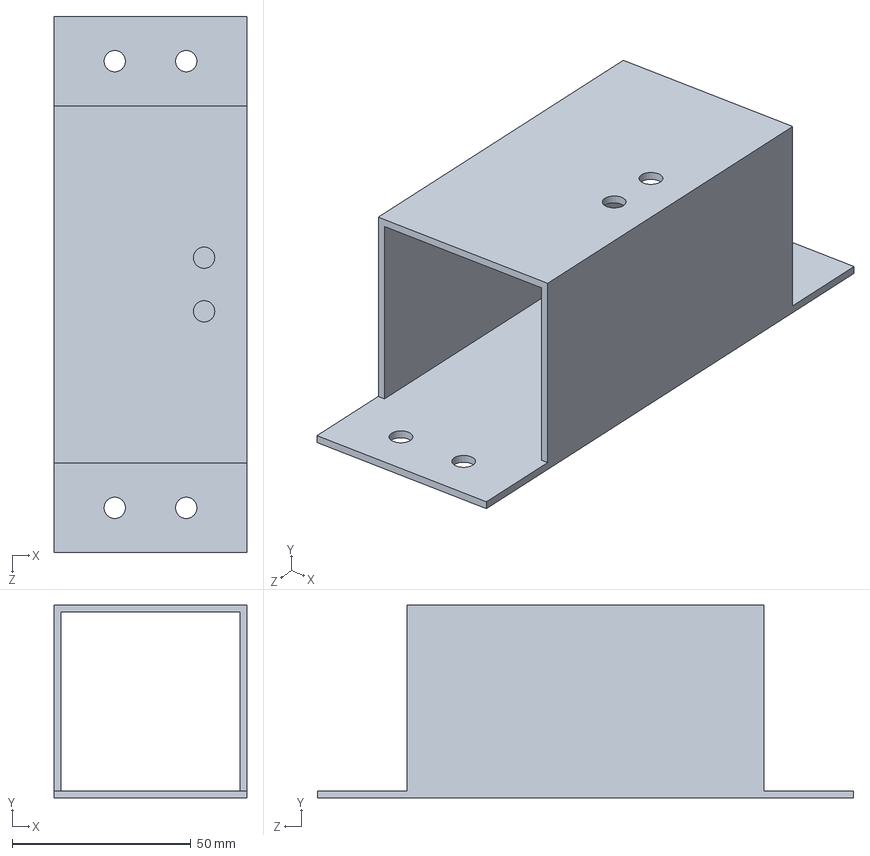
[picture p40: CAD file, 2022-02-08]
Test Stand/CAD design/Cut SHS.SLDPRT
54.0 x 54.0 x 150.0 mm

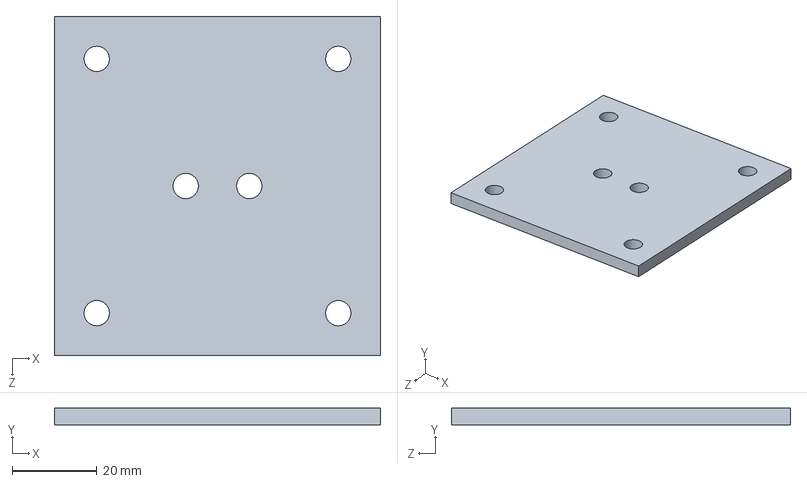
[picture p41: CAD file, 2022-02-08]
Test Stand/CAD design/thrust base.SLDPRT
77.0 x 4.00 x 80.0 mm

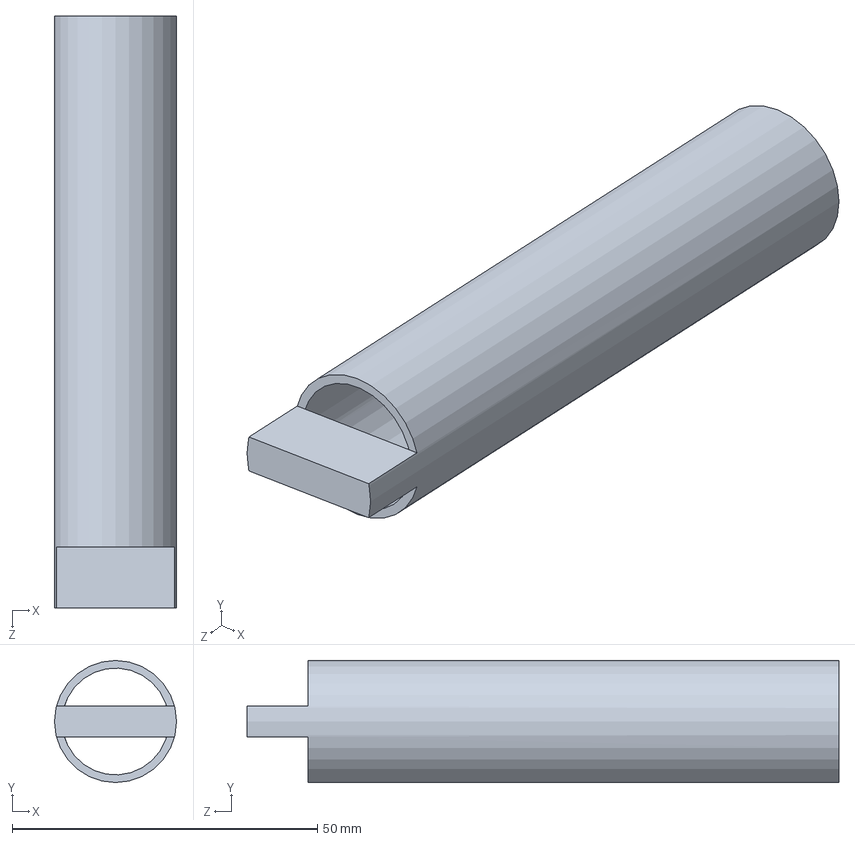
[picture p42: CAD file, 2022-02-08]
Test Stand/CAD design/EMT.SLDPRT
20.0 x 20.0 x 97.0 mm

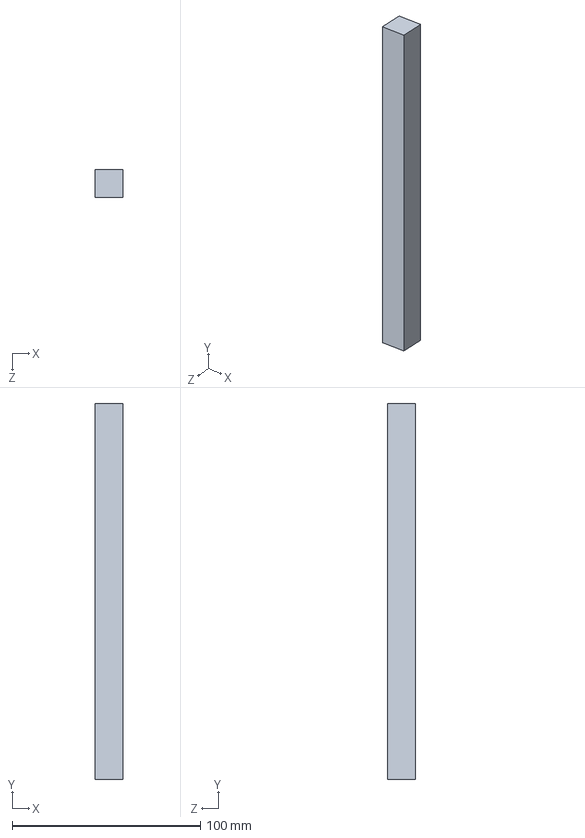
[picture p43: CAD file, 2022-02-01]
Test Stand/CAD design/support.SLDPRT
15.0 x 200.0 x 15.0 mm

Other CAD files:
Fuel/Casting/Casting tools/Part1.SLDPRT
Fuel/Nozzle Designs/Nozzle.dwg
Launch/bulkhead.dwg
Launch/nozzle-1.dwg
Test Stand/CAD design/thrust plate v2.SLDPRT
Fuel/Casting/Casting tools/bottom plate v1.ipt
Fuel/Casting/Casting tools/casting cylinder v3.ipt
Fuel/Casting/Casting tools/compression spring v1.ipt
Fuel/Casting/Casting tools/coring rod pin v1.ipt
Fuel/Casting/Casting tools/coring rod v1.ipt
Fuel/Casting/Casting tools/top bush v1.ipt
Fuel/Casting/Casting tools/washer.SLDPRT
Fuel/Nozzle Designs/Nozzle design v3.ipt
Launch/bulkhead.ipt
Launch/nozzle.ipt
Test Stand/CAD design/base.SLDPRT
Test Stand/CAD design/test stand.SLDASM
Test Stand/CAD design/test stand.dwg
Test Stand/CAD design/thrust plate v2.STL
Test Stand/CAD design/thrust plate.SLDPRT
Test Stand/electronics bay/Cover v2.stl
Test Stand/electronics bay/Electronics bay v14.stl
Test Stand/electronics bay/Electronics bay v6.stl
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

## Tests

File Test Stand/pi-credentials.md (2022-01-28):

## Raspberry PI credentials

# Raspberry PI login
* login as: *pi*
* password: *nakuja1234*

# Default Raspberry PI IP address
*http://192.168.43.31/

# WIFI Credentials stored in Raspberry PI
* ssid : *Faiba4G*
* password : *Ask Washington*

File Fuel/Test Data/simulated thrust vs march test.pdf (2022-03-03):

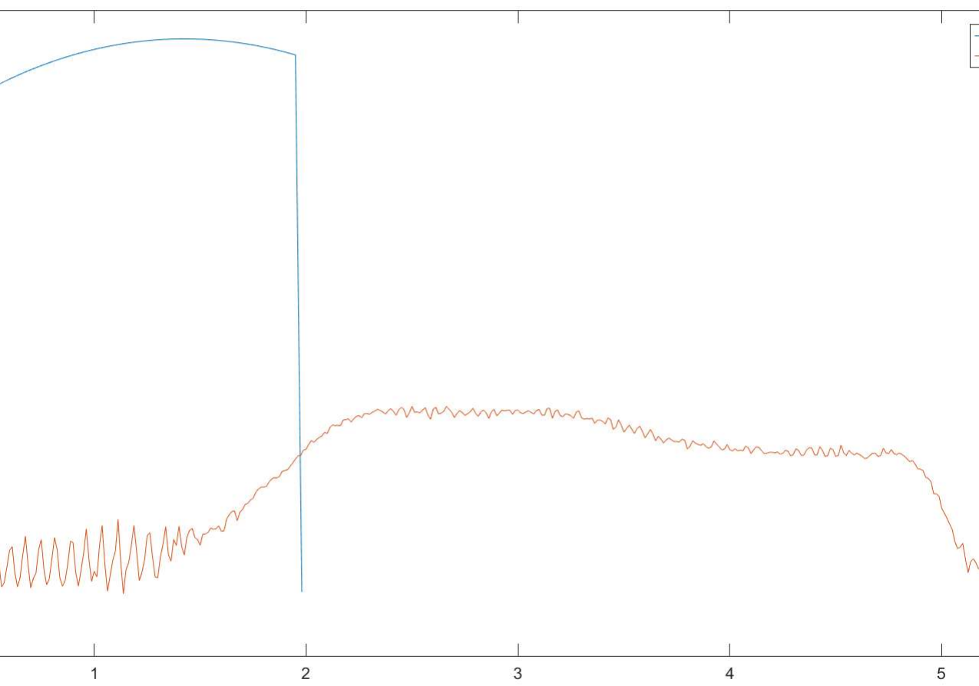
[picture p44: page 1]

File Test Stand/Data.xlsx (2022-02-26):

Mass | Thrust | Time
0.9 | 0.008829 | 0.0125
1.2 | 0.011772 | 0.025
0.8 | 0.007848 | 0.0375
0.6 | 0.005886 | 0.05
0.9 | 0.008829 | 0.0625
0.8 | 0.007848 | 0.075
0.6 | 0.005886 | 0.0875
-0.8 | -0.007848 | 0.1
-0.7 | -0.006867 | 0.1125
0.9 | 0.008829 | 0.125
0.1 | 0.000981 | 0.1375
1.2 | 0.011772 | 0.15
1 | 0.00981 | 0.1625
0.1 | 0.000981 | 0.175
0.7 | 0.006867 | 0.1875
0.4 | 0.003924 | 0.2
1 | 0.00981 | 0.2125
1 | 0.00981 | 0.225
-0.2 | -0.001962 | 0.2375
-0.6 | -0.005886 | 0.25
0.3 | 0.002943 | 0.2625
1 | 0.00981 | 0.275
0.9 | 0.008829 | 0.2875
0.6 | 0.005886 | 0.3
0.9 | 0.008829 | 0.3125
-0.8 | -0.007848 | 0.325
0 | 0 | 0.3375
1.3 | 0.012753 | 0.35
1.1 | 0.010791 | 0.3625
1.7 | 0.016677 | 0.375
1.5 | 0.014715 | 0.3875
-0.5 | -0.004905 | 0.4
-1.8 | -0.017658 | 0.4125
-1.1 | -0.010791 | 0.425
-0.7 | -0.006867 | 0.4375
0.8 | 0.007848 | 0.45
0.4 | 0.003924 | 0.4625
-0.5 | -0.004905 | 0.475
0 | 0 | 0.4875
1.7 | 0.016677 | 0.5
1.6 | 0.015696 | 0.5125
0.8 | 0.007848 | 0.525
0.3 | 0.002943 | 0.5375
1.4 | 0.013734 | 0.55
1.5 | 0.014715 | 0.5625
1.4 | 0.013734 | 0.575
1.5 | 0.014715 | 0.5875
1.1 | 0.010791 | 0.6
0.5 | 0.004905 | 0.6125
0.5 | 0.004905 | 0.625
1.1 | 0.010791 | 0.6375
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

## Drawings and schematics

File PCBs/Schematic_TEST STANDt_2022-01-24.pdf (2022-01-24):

## ignition

## Power

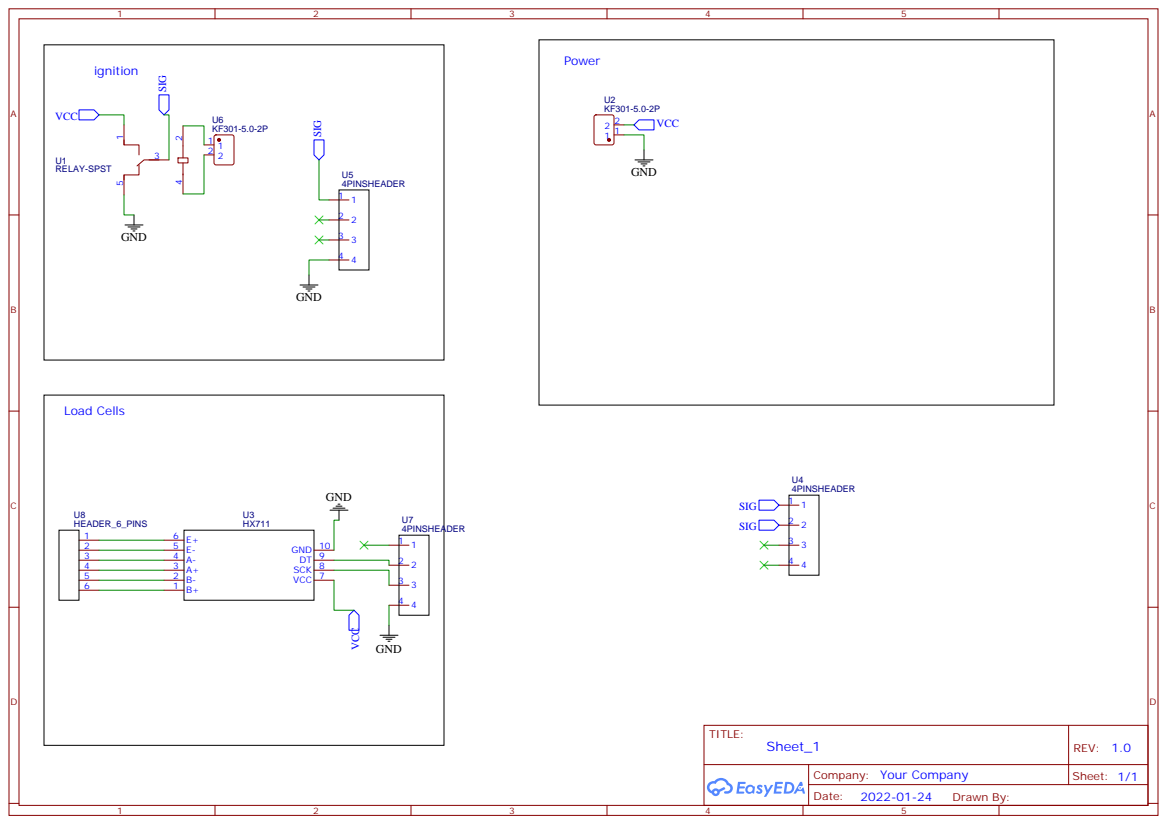
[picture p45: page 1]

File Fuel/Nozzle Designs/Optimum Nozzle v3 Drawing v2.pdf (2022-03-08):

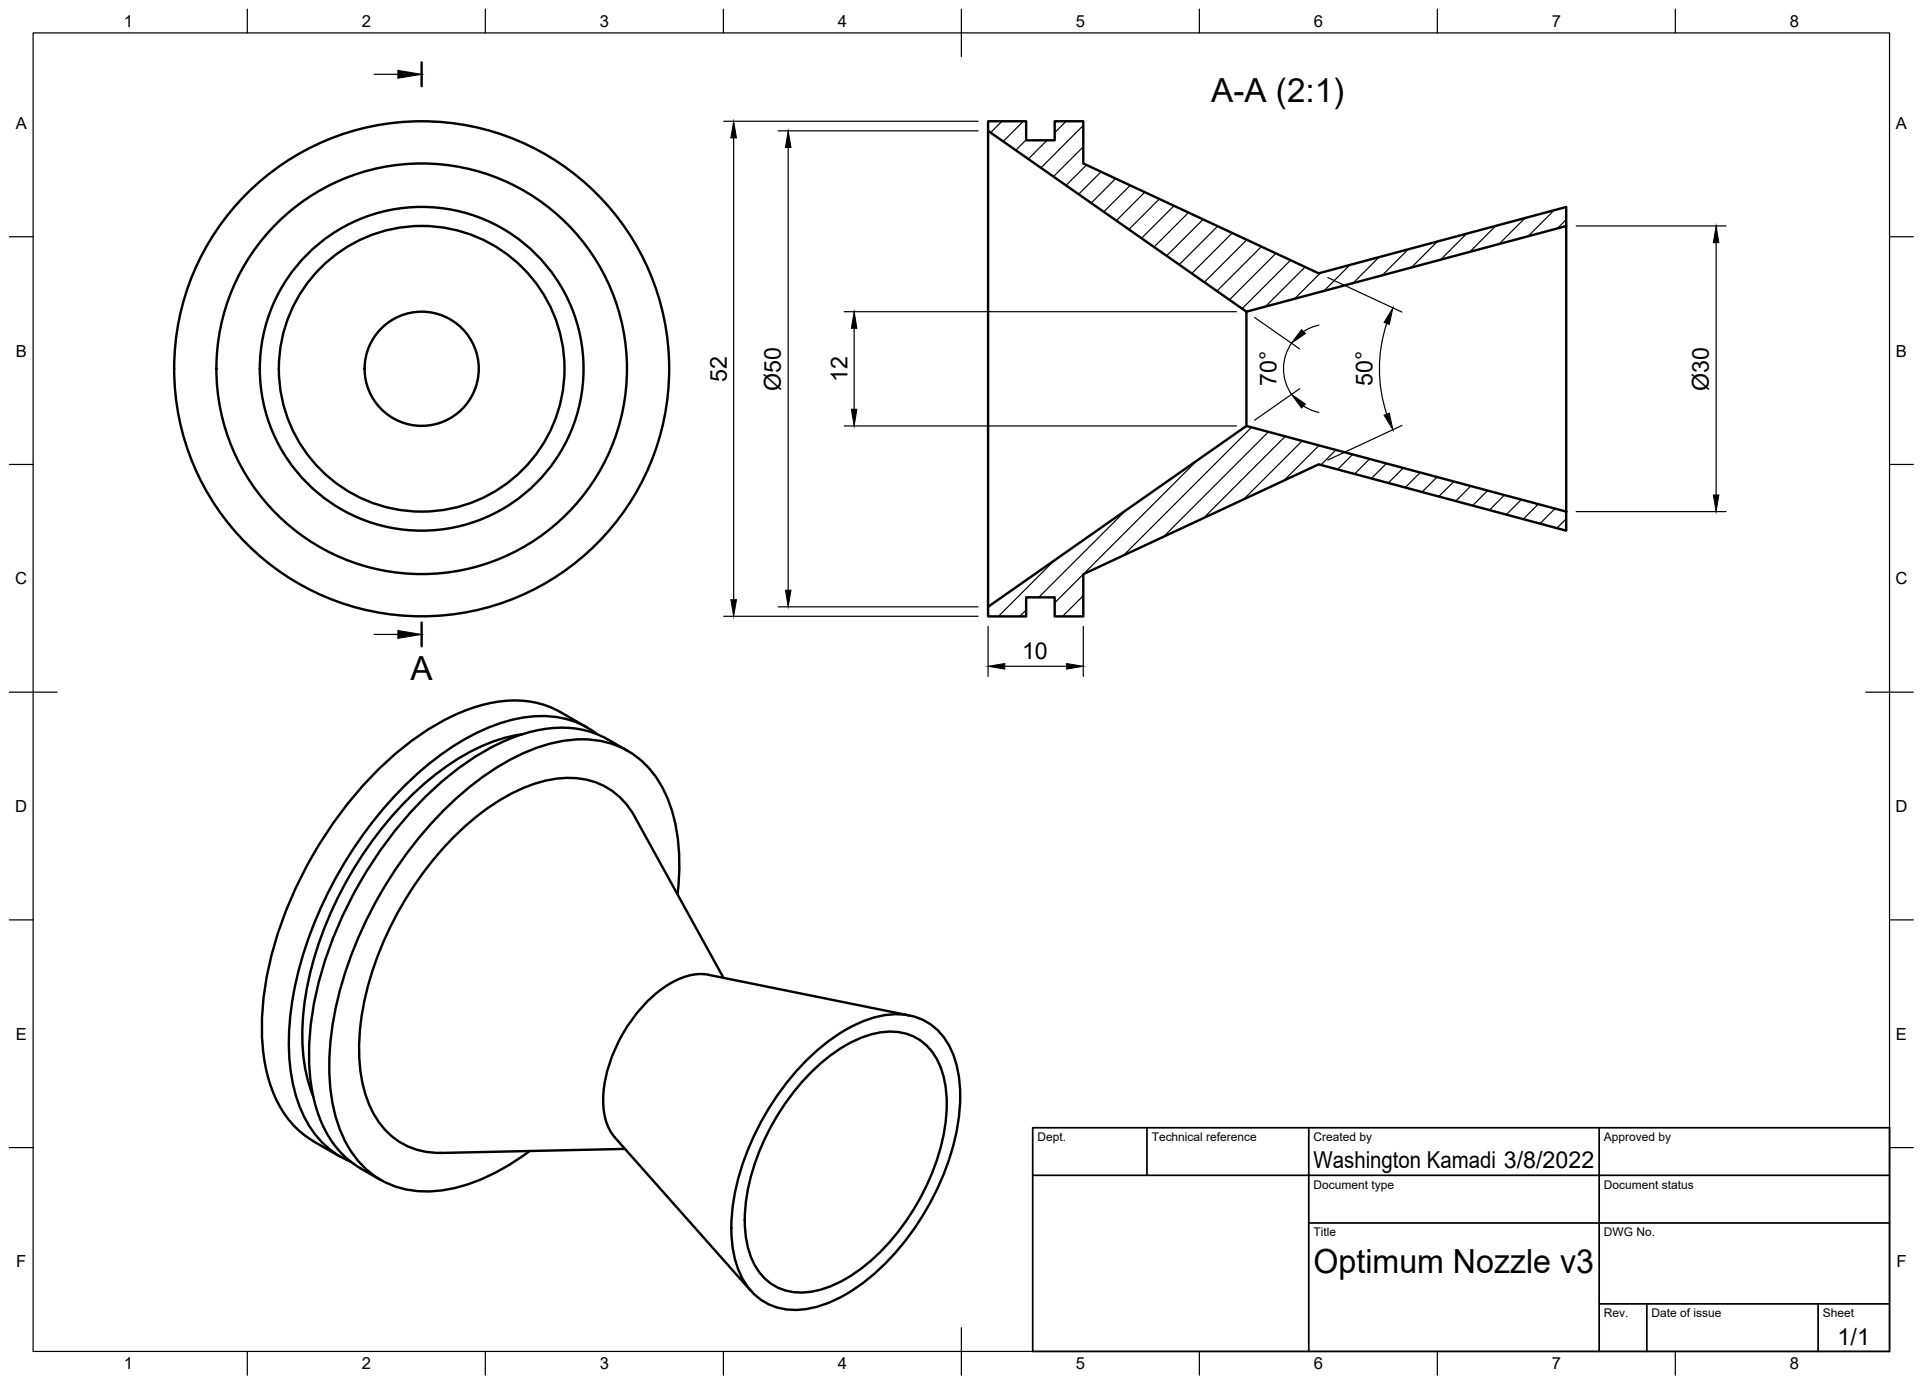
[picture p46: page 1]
Title; DWG No.; Rev.; Date of issue; Sheet; Optimum Nozzle v3

Dept. | Technical reference | Created by Washington Kamadi 3/8/2022 | Approved by

Document type | Document status

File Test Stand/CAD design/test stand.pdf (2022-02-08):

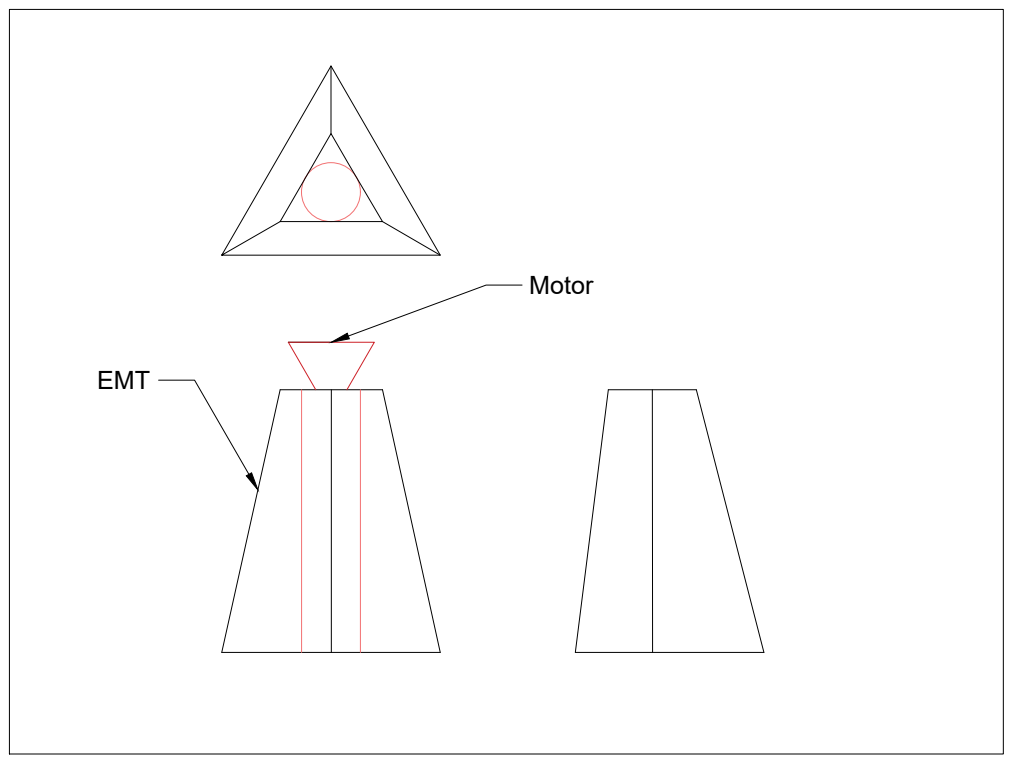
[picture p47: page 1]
Motor EMT

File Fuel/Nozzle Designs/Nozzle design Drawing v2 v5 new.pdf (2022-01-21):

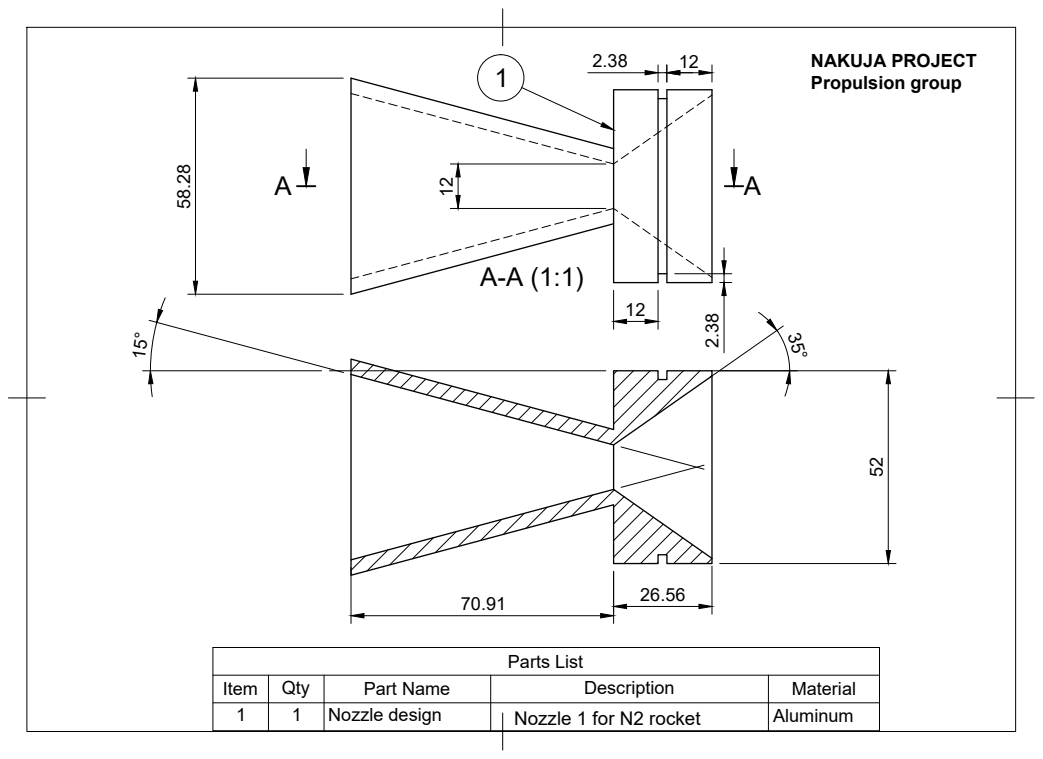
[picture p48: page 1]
NAKUJA PROJECT Propulsion group; Parts List

Item | Qty | Part Name | Description | Material
1 | 1 | Nozzle design | | | Aluminum

Nozzle 1 for N2 rocket

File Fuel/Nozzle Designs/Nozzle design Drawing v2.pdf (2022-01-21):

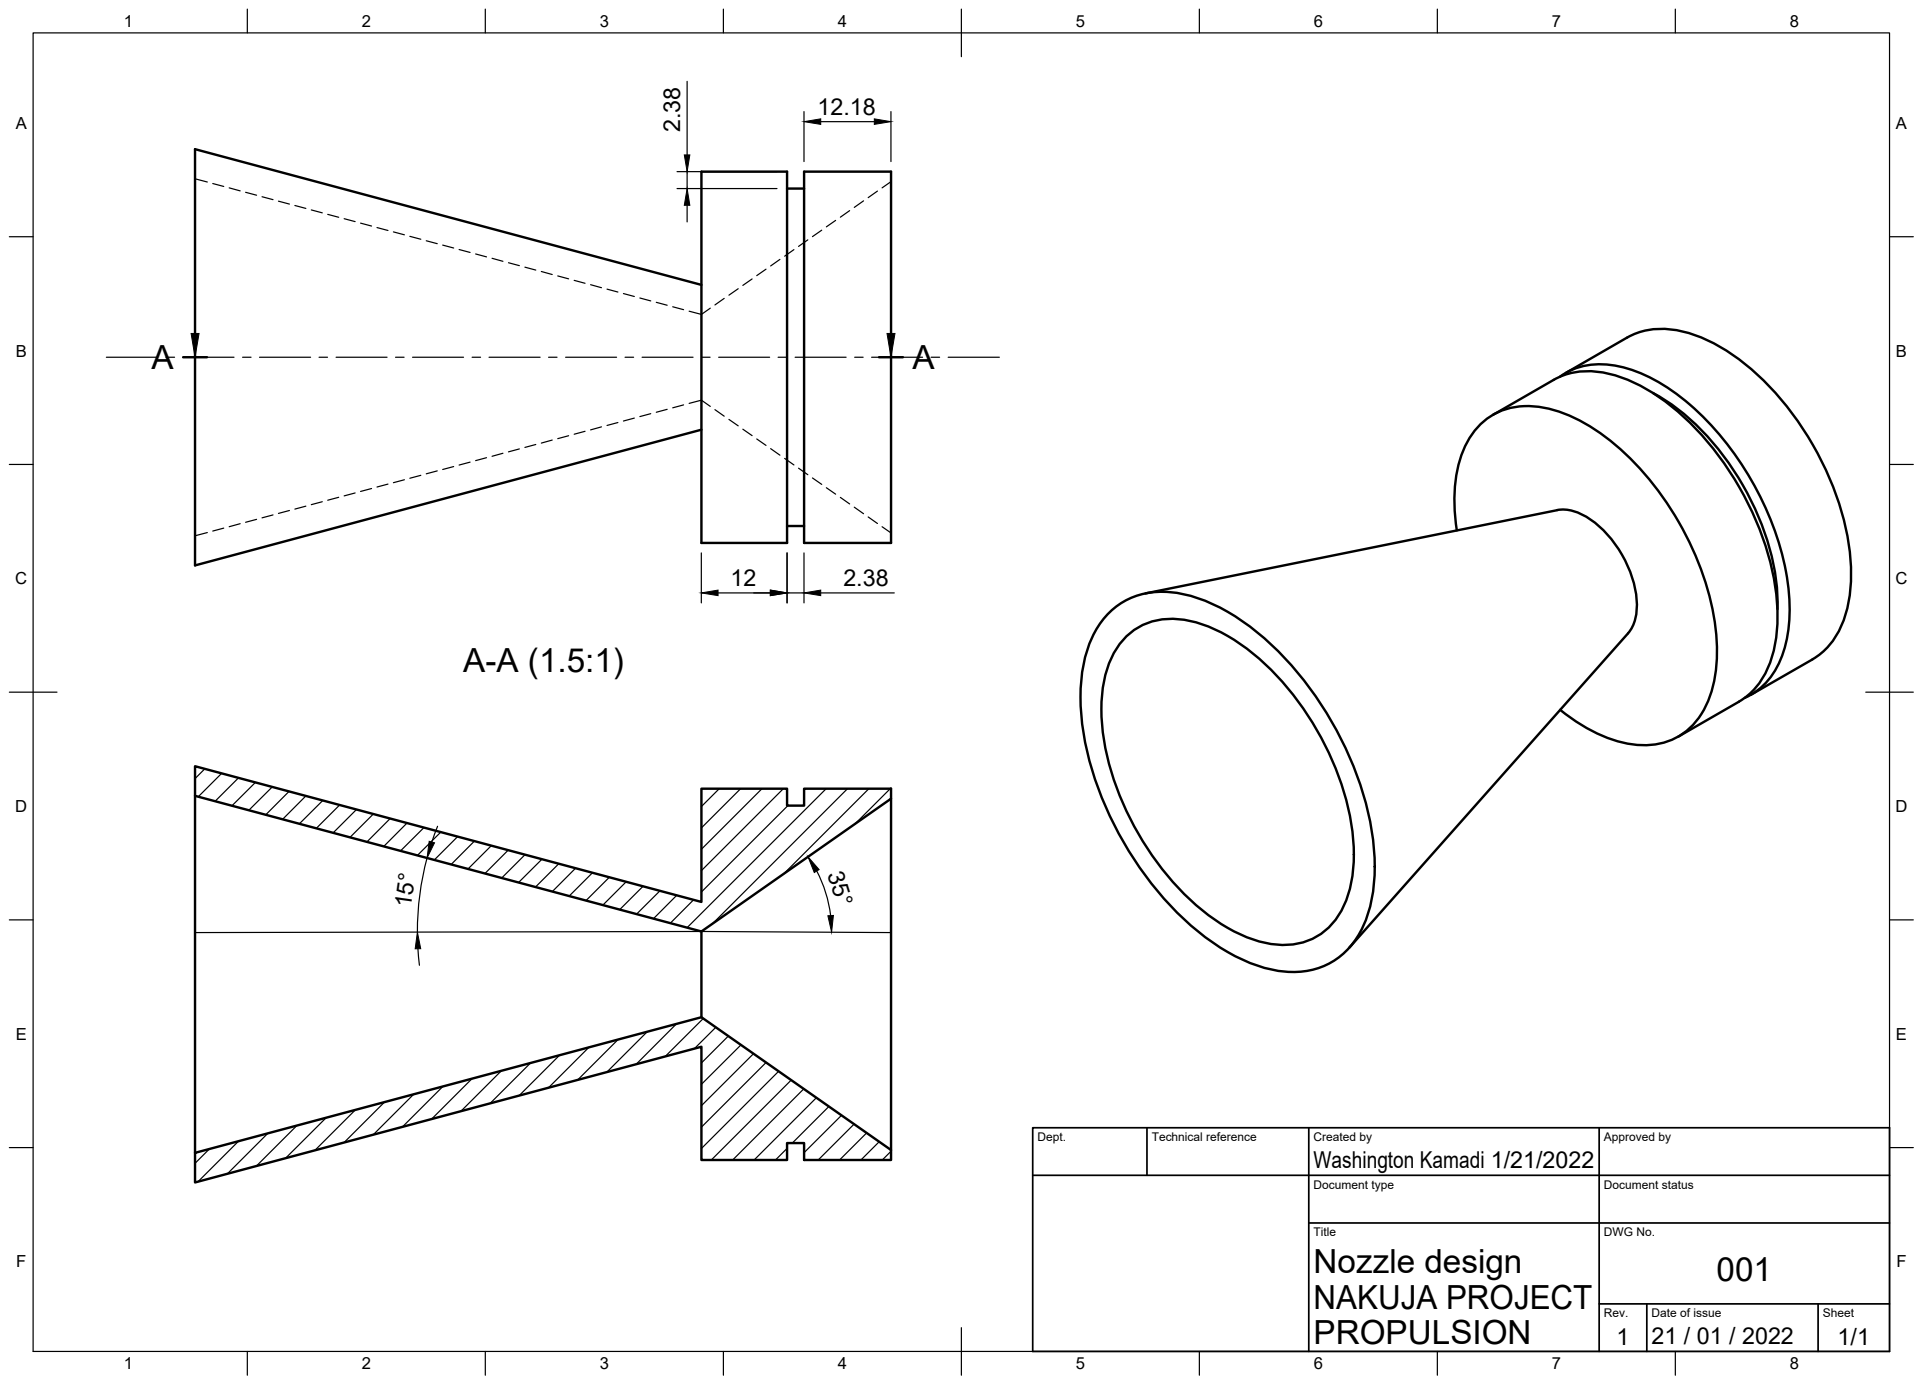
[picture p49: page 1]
Title; DWG No.; Rev.; Date of issue; Sheet; PROPULSION; NAKUJA PROJECT; Nozzle design

Dept. | Technical reference | Created by Washington Kamadi 1/21/2022 | Approved by

Document type | Document status

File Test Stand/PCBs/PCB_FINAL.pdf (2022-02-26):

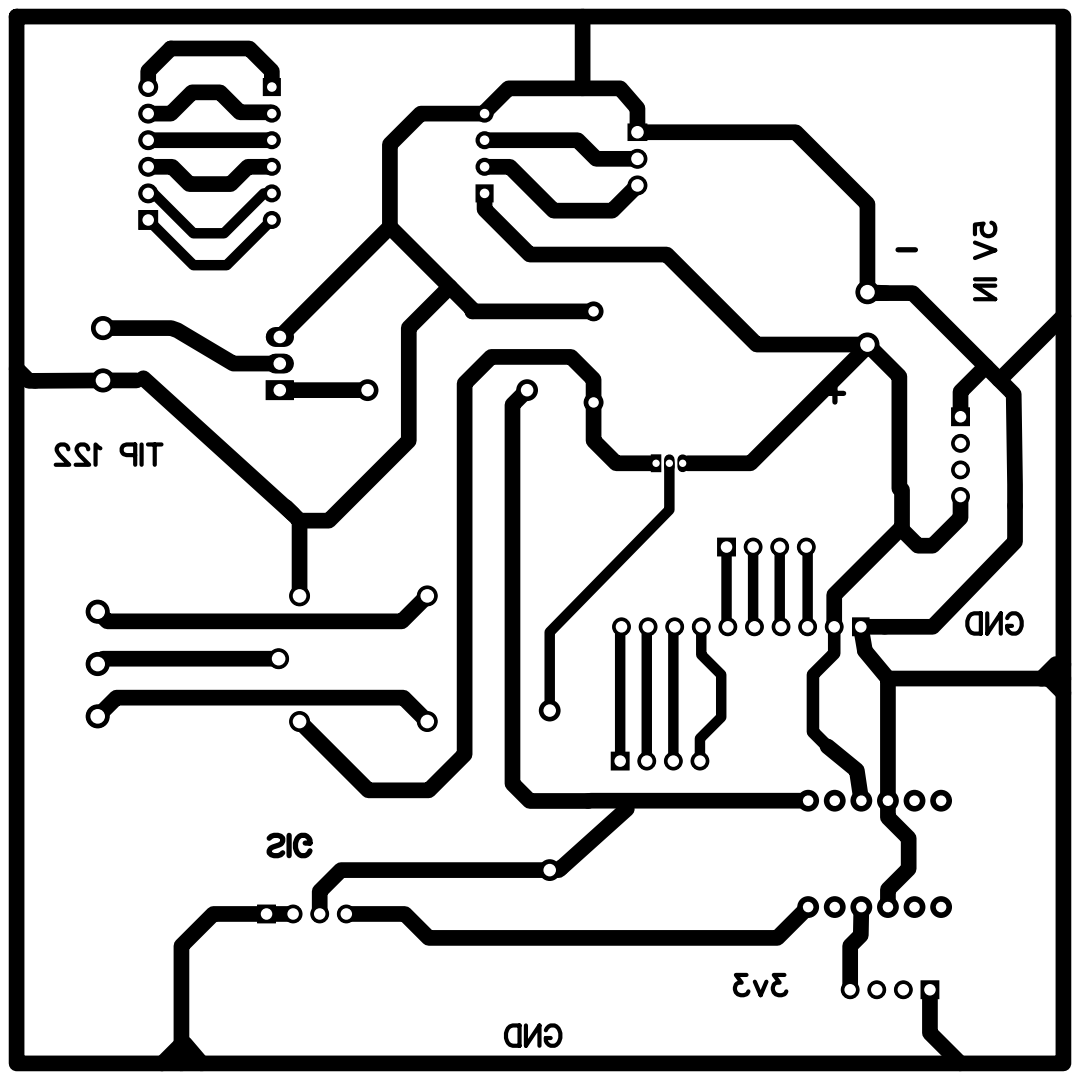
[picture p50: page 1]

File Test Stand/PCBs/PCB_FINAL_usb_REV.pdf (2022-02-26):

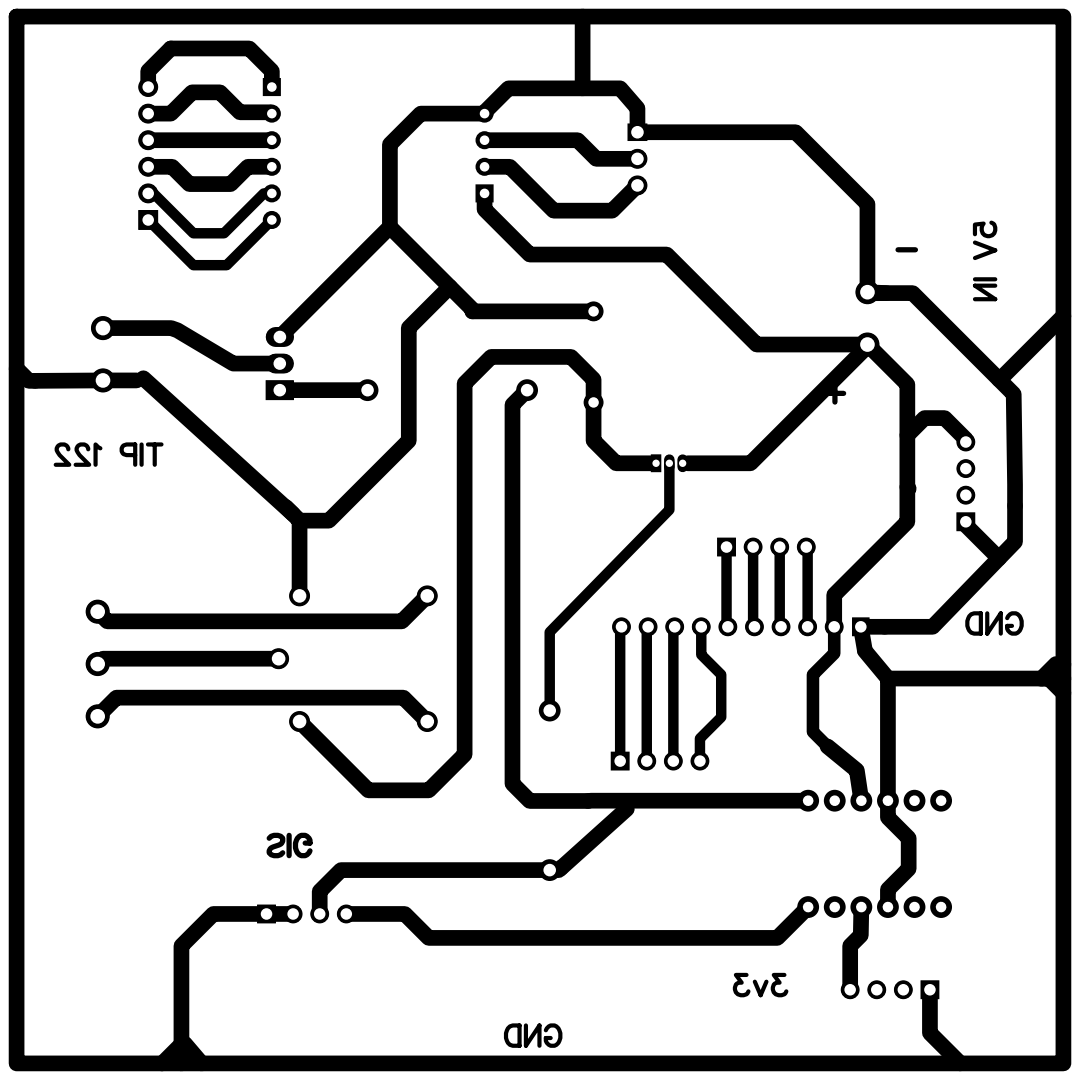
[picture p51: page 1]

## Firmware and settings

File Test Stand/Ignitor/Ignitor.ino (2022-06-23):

int ignite = 0;

int tst, prevIgnite;

void setup() {
  // put your setup code here, to run once:
  Serial.begin(9600);
  pinMode(8, OUTPUT);
  //const_val = analogRead(A0);
  digitalWrite(8, HIGH);
  //Serial.println(const_val);
  delay(30000);
}

void loop() {
  // put your main code here, to run repeatedly:
  
  /*ignite = analogRead(A0);
  Serial.println(ignite);
  tst = abs(ignite - prevIgnite);
  prevIgnite = ignite;
  if ( tst >= 80 ) {*/
    delay(100);
    digitalWrite(8, LOW);
    delay(5000);
    digitalWrite(8, HIGH);
    delay(100);
    //}
}

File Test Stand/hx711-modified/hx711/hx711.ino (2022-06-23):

#include <Arduino.h>
// https://github.com/bogde/HX711
#include "HX711.h"
const int DT_PIN = 6;
const int SCK_PIN = 5;
HX711 scale;
//TO DO
//set reference and offseet
void setup() {
  float unit = 2812.80;
  float reference_i = 221.0;
  float deviation = 3.40;
  Serial.begin(9600);
  //Serial.println("start");
  scale.begin(DT_PIN, SCK_PIN);
  scale.get_units(10);

  scale.set_scale(unit/reference_i); //set reference units
  scale.get_units(10);
  scale.tare();
  scale.get_units(10);

  //scale.set_offset(deviation); //definition of offset?

  scale.get_units(10);
  //Serial.println("here");
}


void loop() {
  Serial.println(String(scale.get_units(1), 1) );
}

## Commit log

2022-01-17 Update structure
    [SRM_2014.1.xls, casing.xls]
2022-01-17 Nozzle designs
    [Nozzle.dwg]
2022-01-18 Create PCB requirements.pdf
2022-01-19 STL files for electronics hub
    [Cover v2.stl, Electronics bay v6.stl]
2022-01-19 Modify print files
    [Cover v3.stl, Electronics bay v14.stl, Electronics bay v16.stl]
2022-01-19 Update Cover v3.stl
    [Cover v3.stl]
2022-01-21 V1 Nozzle designs
    [Nozzle design v3.ipt]
2022-01-21 Nozzle optimisation simulation
2022-01-24 Nozzle design update
2022-01-24 Create PCB
2022-01-26 adding casting tolls ipt files
    [bottom plate v1.ipt, casting cylinder v2.ipt, compression spring v1.ipt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]
2022-01-27 Added more software
    [EzImpulse_v1.0.xlsm, ezalt_1.3.xls, ezrocket.xls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]
2022-01-27 updating casting tools
    [casting cylinder v2.ipt, casting cylinder v3.ipt]
2022-02-08 Test stand
    [Cut SHS.SLDPRT, EMT.SLDPRT, SHS Aluminum.SLDPRT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]
2022-03-08 Nozzle Design considerations
2022-03-08 Optimum nozzle drawing
2022-03-08 Update NOZZLE DESIGN CONSIDERATIONS.pdf
2022-06-23 Simulated motor
2022-06-23 Create Rocket Skeleton.SLDPRT
    [Rocket Skeleton.SLDPRT]
2022-06-23 3d Printing skeleton
    [Rocket Skeleton.STL]
2022-07-06 Modified motor
    [thrust plate v3.STL]
2022-08-24 Update cfd
    [Scenario 1.csv]
2022-11-14 Nozzle design
    [nozzle-1.dwg, nozzle.ipt]
2022-11-14 Bulkhead design
    [bulkhead.dwg, bulkhead.ipt]
2022-11-21 Calibration factor
